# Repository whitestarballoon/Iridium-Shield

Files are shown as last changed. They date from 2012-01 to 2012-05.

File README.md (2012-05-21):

Iridium 9602 Satelite Modem Shield
==============

This Arduino/Netduino shield will interface an Iridium 9602 SBD Satellite Modem, transmitting small binary (or text) data messages to or from anywhere in the world. (340 bytes from modem to Internet, 270 bytes to modem from Internet)  It's been tested in the field to provide 2-way telemetry and control communications on long-duration weather balloon flights for http://whitestarbaloon.com.  

If you'd like your own shield PCB, feel free to use the Gerber directory to have a copy made, or email <info@whitestarballoon.org> for more info.

This shield is designed using the KiCad Software.

For Arduino code that we used with this shield, see the [White Star Comm-Controller github repository](https://github.com/whitestarballoon/Com-Controller).  Flight tested!

Features
-------------

- U.FL connector for antenna
- [Pololu Voltage Regulator](http://www.pololu.com/catalog/product/2110) header for supplying clean power to 9602
- Super Capacitors to Decouple Transmit Spike (5V @ 1.5A for ~10mS during transmission)
- Configurable Serial Lines (Selectable by solder or pin jumpers)

Compatibility
-------------

This shield is compatible with the following platforms:

-  Arduino Mega (Tested with Mega 2560)
-  Seeduino Mega (Untested)
-  Netduino (Untested)
-  Arduino Uno (Untested)
-  Arduino Due (Untested)

Requirements
------------

### Power input
This shield is designed to accept power in 2 different ways, CHOOSE ONLY ONE:

- External 5V regulated, 2A is recommended (as low as 500ma may work with reduced transmit duty cycle) 
  - supply higher power here (no more than 3.5A) here if you experience brownout warnings or want to use a smaller supercap
  - Screw terminals available on the shield
- Arduino/Netduino onboard voltage 5V regulator
  - Transmissions will have to be limited to once every few minutes, to allow supercap to charge
  
### Additional Components Not Included
- Iridium 9602 Modem
  - Bare Iridium 9602 modem modules are available from [NAL Research](http://www.nalresearch.com/IridiumHardware.html) (look for 9602-I).
- Iridium Antenna
  - u.fl to SMA adapter cable 
  - Antennas are available from [NAL Research](http://www.nalresearch.com/IridiumHardware.html).
  - DO NOT OPERATE 9602 MODEM WITHOUT PROPER ANTENNA

Optional Accessories
----------------
- Screw/JST connector for 5V in on shield
- Li-Poly Power Shield

Bill of Materials
----------------
See google doc: [IRShield BOM](https://docs.google.com/spreadsheet/ccc?key=0AnfcbUEovLhOdDBFMjhTX09pdklTWF9EdWd0ZmhmX1E&hl=en_US)

Specifications (actual for Rev 1 pcb)
--------------

Arduino pin numbers:

- Pins D18/D19 for UART1 on Arduino Mega (and similar) *REV 1 PCB swap lines using wire jumpers from JP4 to D18, and JP2 to D19*
- Pins D0/D1 for UART on Arduino Uno/Due and Netduino *REV 1 PCB swap lines using wire jumpers diagonally across JP4 and JP2*
- Pins D7/D8 for SoftSerial (Optional) *REV 1 PCB swap tx/rx in software*
- Pin D2: Message Waiting Indicator (RI, ACTIVE-LOW on Interrupt 0)
- Pin D3: Satellite Available Indicator (NA, ACTIVE-LOW on  Interrupt 1)
- Pin D4: Modem Power Enable (SET HIGH = TURN MODEM ON)
- Pin D5: Brownout Detector Indicator 4.8v (ACTIVE-LOW)
- Pin D6: Modem Bootup Complete Indicator (DSR, ACTIVE-LOW)

Shield LED Labels:

- D1 = (RI) Message Waiting Indicator
- D2 TX = Serial data TO 9602 **CONFUSING**
- D3 RX = Serial data FROM 9602 **CONFUSING**
- D4 = 5V Power ON
- D5 = (NA) Satellite Available 

Theory of operation
-------------------

### Modem Module Power Requirements 
These requirements should be met by the shield circuitry itself, and are different from the shield input power requirements.  Meeting the requirements that White Star has defined for the shield will allow the shield to take care of the modem properly.  

9602 Input Voltage range: 5.0V DC ±0.5V
9602 Input Voltage Ripple: <40mV pp

- The supply voltage droop over for a 8.3ms burst of 1.5A current should not be more than 0.2 Volts. 
- The power supply should limit the in-rush2 current to 4 Amps maximum
- The power source shall provide for over current protection in case of device malfunction.
- The supply noise should be less than the limits in the following profile:
    100 mVpp   from 0 to 50kHz
	5 mVpp     at 1 MHz measured in 50 kHz bandwidth
	10 mVpp    at 1 MHz measured in 1MHz bandwidth
	5 mVpp     above 5 MHz measured in 1 MHz bandwidth

9602 Power Consumption (Typical, depending on antenna and satellite view)
	45mA
	195mA
	1.5A 	Transmit Current peak
	190mA 	Transmit Current average
	195mA 	Receive Current peak
	45mA 	Receive Current average
	190 mA 	Message Transfer average current 
	<= 1.0W Message Transfer average power
Note: More power will be drawn by an antenna that has a high VSWR (poorly matched) 

### Onboard Power Supply Circuit

The power supply circuitry is design to provide the requirements of the 9602.  Due consideration in selecting an external power supply for arduino is necessary.

License
-------


This work is licensed under a [Creative Commons Attribution-ShareAlike 3.0 Unported License](http://creativecommons.org/licenses/by-sa/3.0/).

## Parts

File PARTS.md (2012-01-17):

Parts for Satellite Modem Shield
================================

Parts for this device aren't always easy to find. Satellite Modems are picky about everything.

Power Capacitors
----------------

The 9602 requires very clean power, with good decoupling. We use a mix of standard decoupling caps, and super caps.

Supercapacitors recommended are >0.5F, >=5.4V, <=.5Ω ESR.
We use Caps rated to -40c for flight.

Recommended Power Caps:

- [Illinois Capacitor 155DCN5R4Q](http://octopart.com/255dcn5r4q-illinois+capacitor-8159693)
  - 5.4V
  - 1.5F
  - 200 mΩ ESR
- [Illinois Capacitor 255DCN5R4Q](http://octopart.com/255dcn5r4q-illinois+capacitor-8159858)
  - 5.4V
  - 2.5F
  - 130 mΩ ESR

Power Regulator
---------------

The Arduino 5v regulator cannot supply nearly enough power. The board includes a footprint for this 5v Point-of-Load Power Adapter.

- [Pololu Voltage Regulator](http://www.pololu.com/catalog/product/2110)

Power Brownout Detector
---------------

If the power drops below 4.8v during transmit, the sat modem may fail to function properly (reboot), or messages may simply fail to transmit.  The brownout detector will reliably alert the user of this condition. 
We are using the Rohm BD4848 for this purpose.

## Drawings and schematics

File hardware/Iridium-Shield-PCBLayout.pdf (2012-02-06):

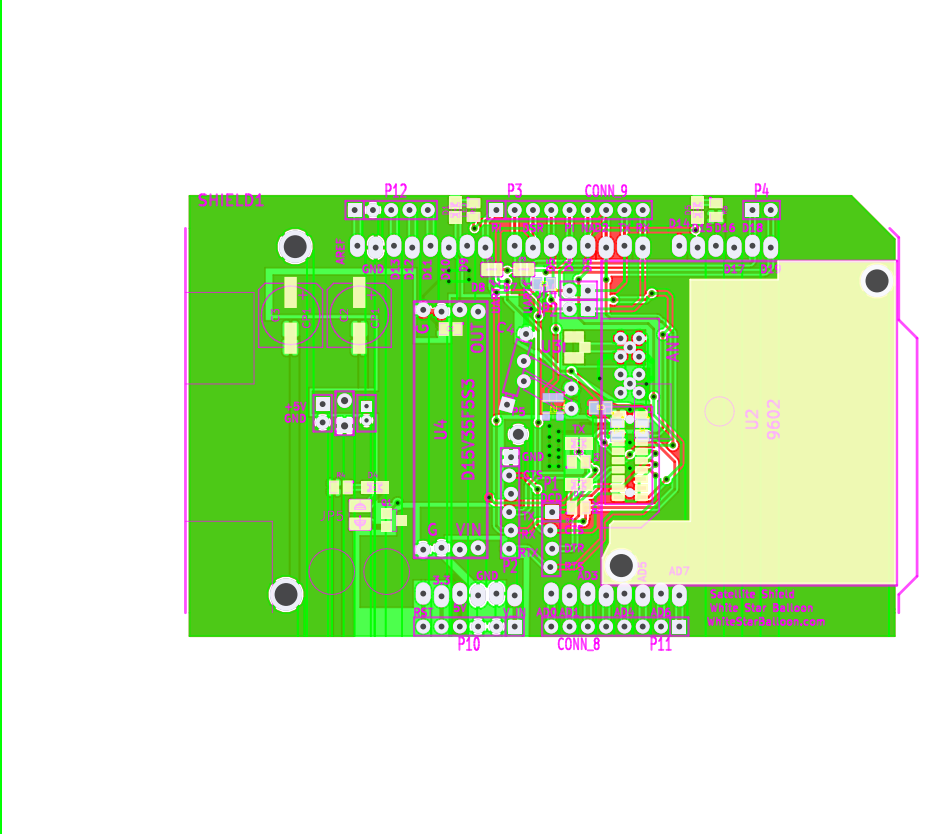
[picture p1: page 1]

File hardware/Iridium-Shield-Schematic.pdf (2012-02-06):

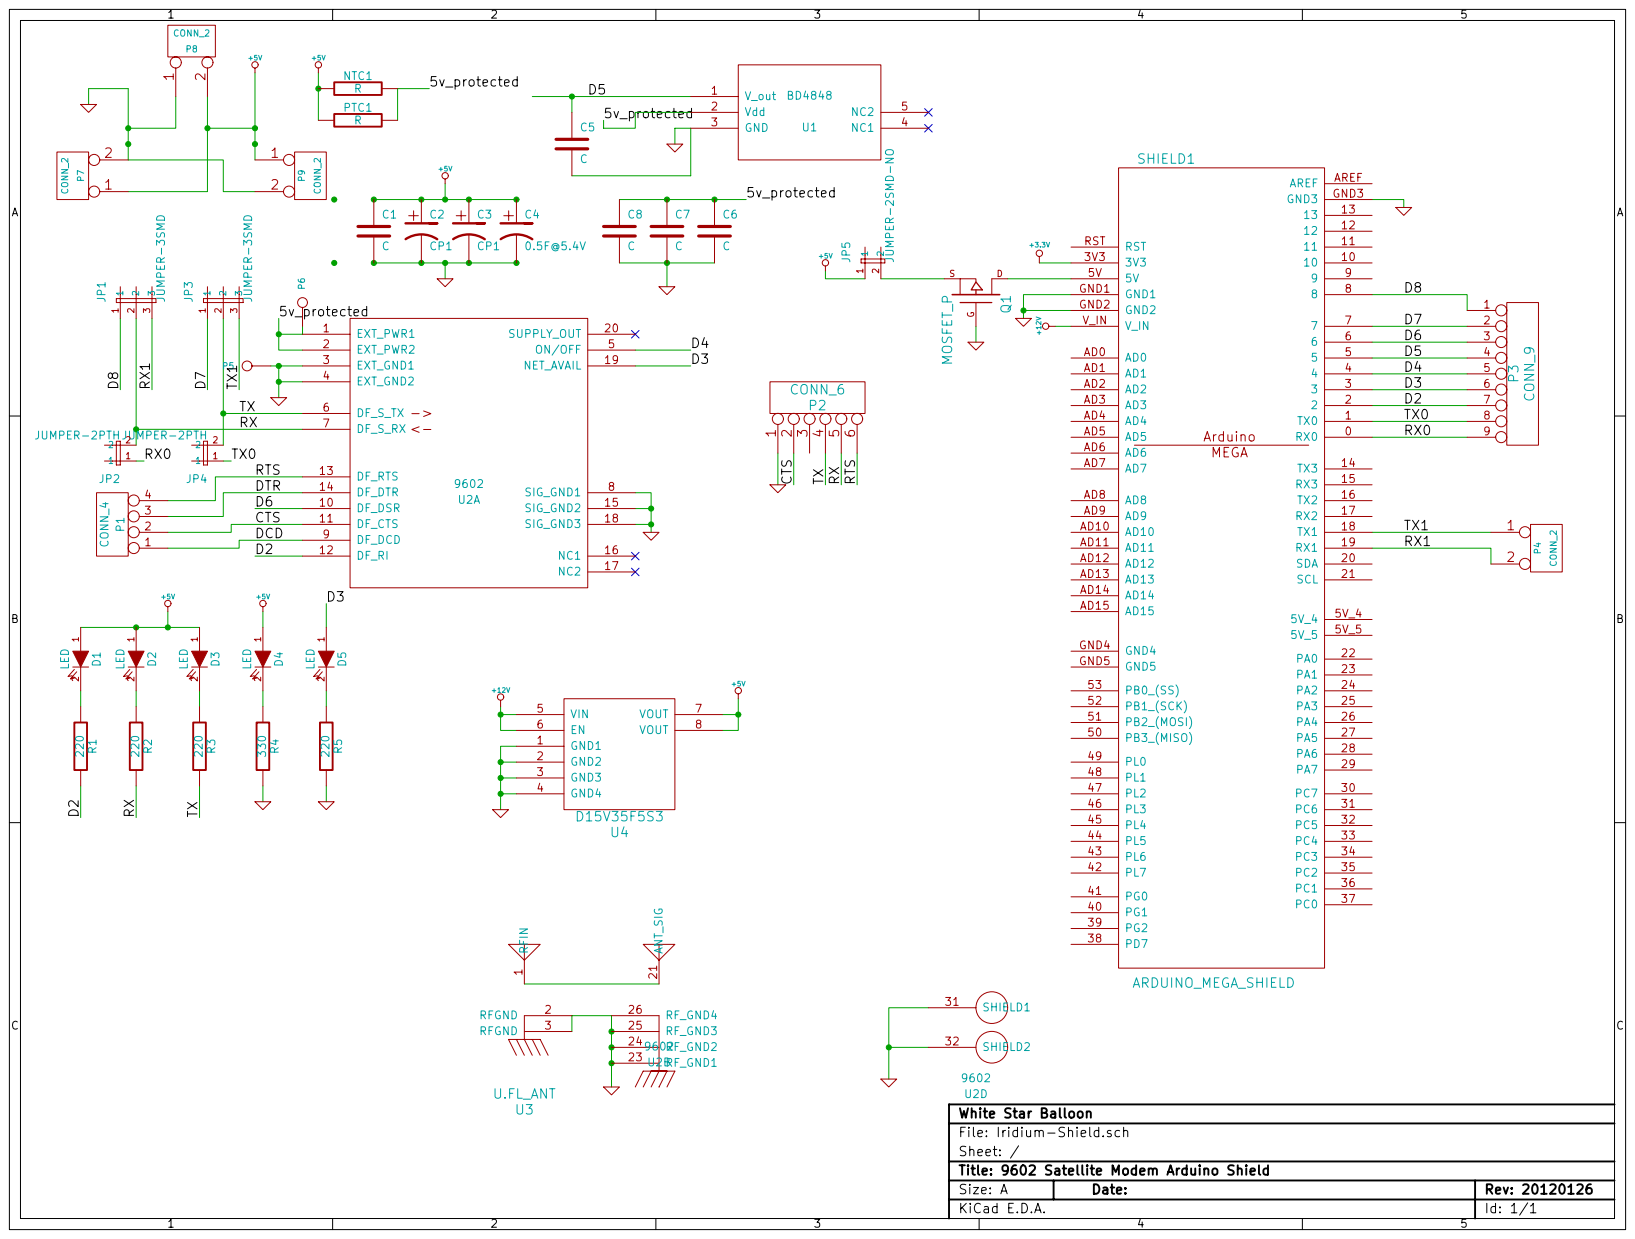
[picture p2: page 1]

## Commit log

2012-01-12 Opened KiCad Project
    Opened KiCad Project, imported, updated and cleaned up 9602 Satellite Modem Footprint.
    Uses 2 MMCX Female Connectors, 1x SamtekCLP-110-02-L-D
    Fixes #2
2012-01-12 Added U.FL Connector to library
    Fixes #3
2012-01-13 Opened Schematic
    Schematic is started.
    [Iridium-Shield.sch]
2012-01-13 Wired up UARTS
    Also added sparkfun headers.
    [Iridium-Shield.sch]
2012-01-13 Schematic Tentatively Complete
    Let's see.
    [Iridium-Shield.sch]
2012-01-13 Schematic Small Tweaks
    For some reason, shield connectors disappeared.
    [Iridium-Shield.sch]
2012-01-13 Began Schematic Capture
    Includes starting to lay components out, start on modifying shield footprint.
    [Iridium-Shield.brd, Iridium-Shield.sch]
2012-01-15 First attempt to layout Shield
    Some less than ideal bits: traces crossing at odd angles (only low speed), big gaggle of vias
    to get a power pour from one side to another, etc.
    [Iridium-Shield.brd, Iridium-Shield.sch]
2012-01-15 Added Power details to readme, some small others
    General info, Modem Power reqs, Onboard power circuit notes.
2012-01-16 Added Solder Mask Cutout under satellite modem (as much as I could.
    No telling how well HASL will work from the board house, but here we go.
    Fixes #12
    [Iridium-Shield.brd]
2012-01-16 Staggered Pin Headers
    Dan, I wan't you to know how much of a pain in the ass that was:
    KiCad recomputes the endpoints of the wires, and decided that none of the
    traces connected any more, but only let me see tiny little air wires.
    Fixes #9
    [Iridium-Shield.brd]
2012-01-17 Changed Brownout Detector, Added Reverse Bias Protection.
    Fixes #13 and #10.
    [Iridium-Shield.brd, Iridium-Shield.sch]
2012-01-17 Changed 9602 footprint to add 4-40 nut spin clearances
    Will need to figure out how to remove analog pins or try putting screw
    head on board bottom.
    [Iridium-Shield.brd]
2012-01-17 Minor Changes
    Added pins near satellite modem to Fix #18.
    Removed thermal relief in a few places, Fixing #15.
    Added slightly more ground pour around RF connectors, though "more" is a nebulous specifier, Fixing #14.
    [Iridium-Shield.brd, Iridium-Shield.sch]
2012-01-20 Fixing Minor Problems
    Added PTC/NTC In series, fixes #11.
    Added SMD Caps, fixes #16.
    Added bunch of connectors, fixes #17.
    [Iridium-Shield.brd, Iridium-Shield.sch]
2012-01-20 Added Gerbers
    [Iridium-Shield-Back.gbl, Iridium-Shield-Front.gtl, Iridium-Shield-Mask_Back.gbs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]
2012-01-20 Updated power requirements to describe 3 ways of powering the shield to users
2012-01-26 Labels, small tweaks
    [Iridium-Shield-Back.gbl, Iridium-Shield-Front.gtl, Iridium-Shield-Mask_Back.gbs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]
2012-01-28 Added Schematic info block, Schematic PDF and Board Layout PDF
    [Iridium-Shield.sch]
2012-01-28 Added Latest Gerbers
    [Iridium-Shield-Back.gbl, Iridium-Shield-Front.gtl, Iridium-Shield-Mask_Back.gbs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]
2012-01-30 Moved Shield module outline to Drawings from silkscreen layer
    [Iridium-Shield.brd]
2012-01-30 Removed drill files from main directory
    [Iridium-Shield-NPTH.drl, Iridium-Shield.drl]
2012-01-30 Exported Gerbers
    [Iridium-Shield.brd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]
2012-01-30 exporter drill file
    [Iridium-Shield.drl]
2012-01-30 Deleted unneeded gerbers
    [Iridium-Shield-NPTH.drl, Iridium-Shield-SilkS_Back.gbo, Iridium-Shield-SoldP_Back.gbp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]
2012-02-06 Updated Readme to as-built PCB Rev 1
2012-02-06 Revert "Updated Readme to as-built PCB Rev 1"
    This reverts commit d6189403ef859f97e7197a0bf6bababca5751a02.
2012-02-06 Revert "Revert "Updated Readme to as-built PCB Rev 1""
    This reverts commit 863803a2d0479758a9a0be3aad79fb4c5b75df97.
2012-02-06 Clean generated files
    [Iridium-Shield-Back.gbl, Iridium-Shield-Front.gtl, Iridium-Shield-Mask_Back.gbs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]
2012-05-21 Emails and some general info updated, added link to arduino code repository.
